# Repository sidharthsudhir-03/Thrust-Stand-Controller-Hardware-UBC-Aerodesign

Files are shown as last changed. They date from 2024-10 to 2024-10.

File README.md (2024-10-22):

# Thrust-Stand-Controller-Hardware-UBC-Aerodesign

## Overview
The **Thrust Stand Controller** is a hardware project designed for measuring motor performance parameters (thrust, torque, voltage, current) for RC aircraft. This controller helps optimize motor configurations and helps in motor selection for the UBC Aerodesign team's aircraft. The system integrates sensors and microcontroller-based data acquisition to provide reliable performance data.

## Features
- **Thrust and Torque Measurement**: Uses dual HX711 load cell amplifiers to measure thrust and torque from the motor.
- **Power Monitoring**: Integrated voltage and current sensors for real-time power consumption analysis. It is rated for 33V and 55A.
- **Microcontroller (ATMEGA32U4-AU)**: Responsible for interfacing with sensors and controlling PWM signals for the motor's ESC.
- **USB-C Connector**: Provides both power supply and data transfer capabilities.
- **ESC PWM Control**: Allows real-time adjustments of motor speed during tests via a 2-pin header for PWM control.
- **Flexible Design**: Added GPIO pin headers and solder pads for easy expansion and motor connection.

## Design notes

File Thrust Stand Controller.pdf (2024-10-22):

# THRUST STAND CONTROLLER

## Overview

The purpose of the thrust stand controller is to provide detailed measurements of motor performance which helps in motor selection for the aircraft. This controller can measure voltage, current, torque and thrust and can potentially take up to 33V and 55A. The schematic overview of the thrust stand controller is as follows:

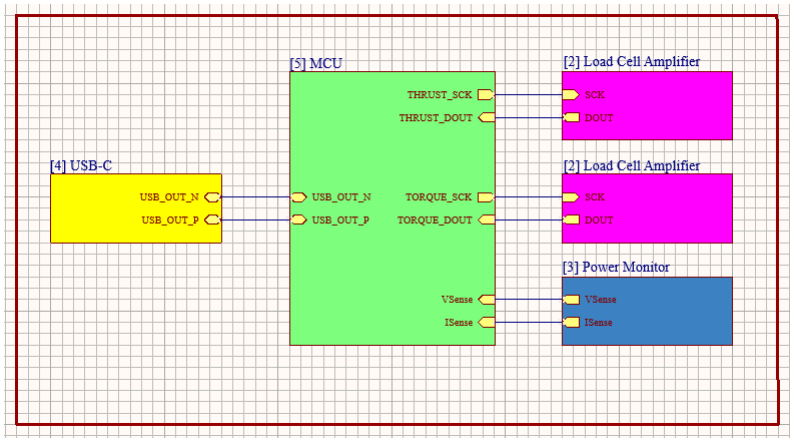
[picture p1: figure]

Fig 1: Top Level Overview of the Schematic
- USB-C: We will be using a USB-C connection for powering up the board and data logging.
- HX711 Load Cell Amplifier: There are two HX711 load cell amplifiers responsible for torque and thrust measurements. Each HX711 measures minute changes in resistance in the load cells, which are directly proportional to the force (thrust or torque). The digital output from the HX711 is fed into the microcontroller for further processing.
- Power Monitor: The power sensor uses a voltage divider circuit followed by an op-amp, which conditions the signal before sending it to the microcontroller's ADC for voltage measurement and a current sense amplifier, which senses the voltage drop across a shunt resistor and amplifies the differential signal to be sent to the microcontroller's ADC, for the current measurement.
- ATMEGA32U4-AU MCU: The ATMEGA32U4-AU microcontroller handles data acquisition from sensors and interfaces with the USB-C. It reads all the signals from the external circuits and processes them. The microcontroller also provides the necessary clock signals for the load cell ADCs (TORQUE_SCK and THRUST_SCK), ensuring synchronized data sampling for both torque and thrust measurements.
- Connections: We have the following connections in the circuit:
- There are 2x11P Male Header Pins on the board for accessing the GPIO pins of the microcontroller, providing flexibility for future expansion, testing or debugging.
- There is a 2P Male Header Pin for sending PWM control directly from the microcontroller to the ESC. One of the pins will be connected to ground.
- There are 2 pairs of solder pads to connect the Power Limiter and the ESC.

The diagram below shows how the thrust stand controller interfaces with external components of the plane’s power system for motor testing:

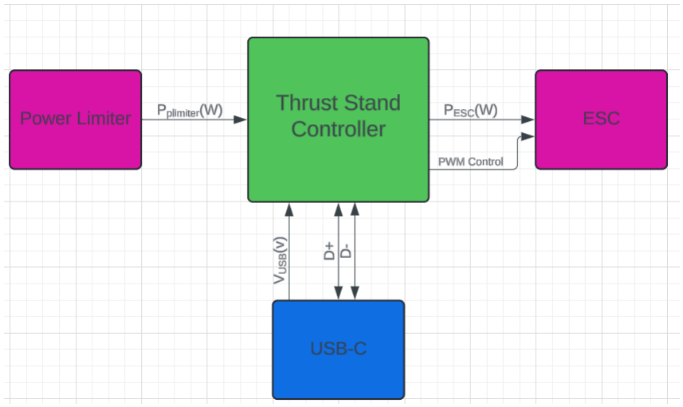
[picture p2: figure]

Fig 2: Thrust Stand Controller Connection Interface with External Hardware

## Sub Circuitry

In the following section, we will go over the main sub circuits of the thrust stand controller in detail and justify design decisions.

### 1. Load Cell Amplifier

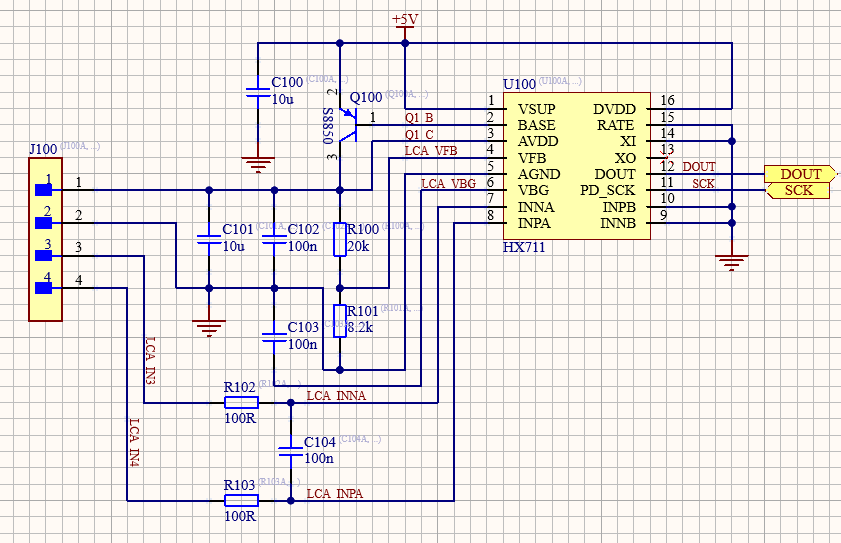
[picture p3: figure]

Fig 3: Load Cell Amplifier Schematic
The load cell amplifier is inspired by the circuitry suggested for the HX711 ADC in the datasheet (Fig.1 and Fig.4 in [1]).

The recommended component values for most of the components in the load cell amplifier is given in the datasheet as well. The only thing needed to be identified is the values of the voltage divider network (R100 and R101 in this diagram). The voltage divider network is crucial for setting the AVDD voltage of the HX711 and the formula is given by:

V

AVDD = V
BG

*

(R

100+R
101

)
R
101

VBG is 1.25V [1]. With the resistor network chosen, we get AVDD voltage as 4.3V, which is suitable for powering the analog portion of the HX711 since it must be slightly lower than VSUP (by at least 100mV) for proper operation [1]. Also note, the formula given for AVDD is incorrect and has

R101 and R100 swapped [2]. The clock for the HX711 will be fed by a GPIO pin of the microcontroller.

### 2. Power Monitor

The power monitor circuitry consists of a voltage sensor and a current sensor which sends data signals to the microcontroller for power measurement. We use solder pads to interface the power limiter and ESC with the microcontroller. The voltage and current from the power limiter is fed into the power monitor and the ESC in this scenario is treated as a load.

a. Voltage Sensor

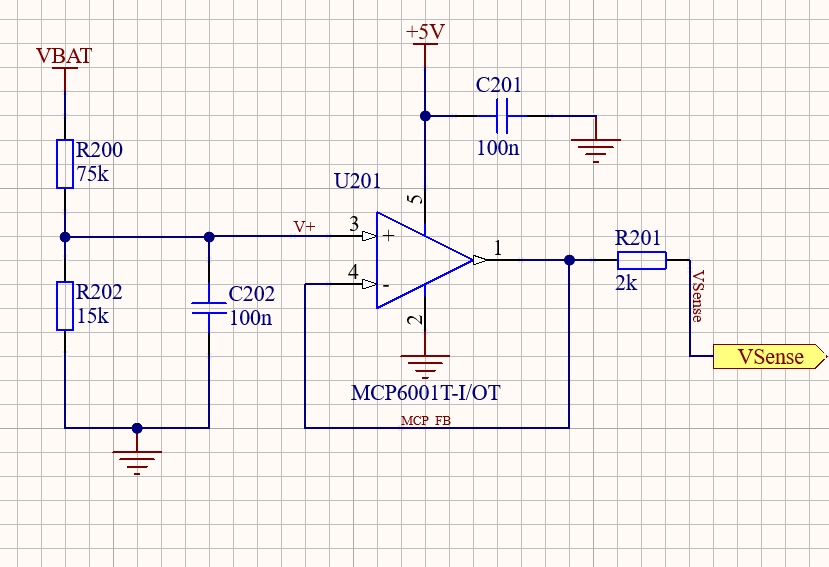
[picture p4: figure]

Fig 4: Voltage Sensor Schematic
The schematic of the voltage sensor consists of a simple voltage divider network followed by a voltage follower circuit and an additional resistor. The values of the voltage divider network was chosen in such a way that the high and low voltage levels of the input (which corresponds to a 6S LiPo) was easily detected by the microcontroller. In other words, we need to scale down a full charge and low charge 6S to a voltage level in the range of 2.7-5.5V (operating voltage range of the microcontroller (Page 2 of [3])). The voltage divider network gives us a scaling ratio of ⅙. This means:

V

VSENSE = V
BAT

*

R
202
R

200+R
202

=

V
BAT
6

A 6S LiPo at full charge is 25.2V and at low charge is 19.2V. When passed through this circuit, we get estimated values for VSense to be 4.2V and 3.2V respectively. With these calculations, we can expect the circuit to take up to 33V maximum (since the microcontroller supports up to 5.5V) This can be backed up by the spice simulations conducted:

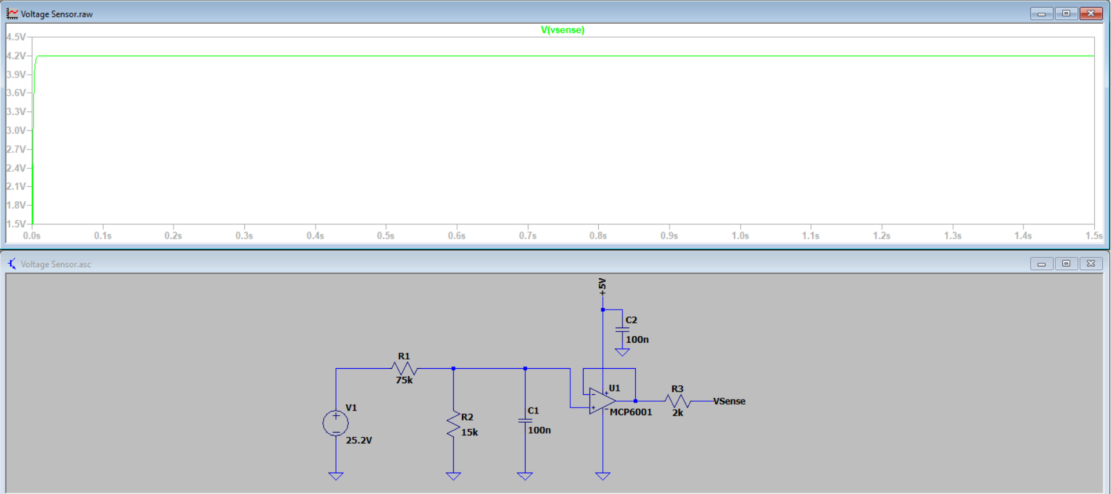
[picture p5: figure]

Fig 5: LTSpice Simulation for Voltage Sensor at 25.2V

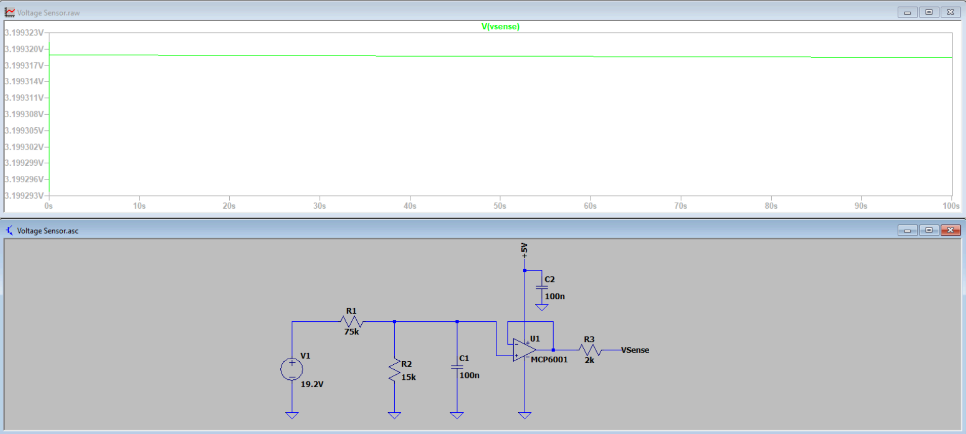
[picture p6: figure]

Fig 6: LTSpice Simulation for Voltage Sensor at 19.2V
The purpose of the capacitor is for decoupling purposes at the input of the opamp. The purpose of the voltage follower and the 2kOhm resistor is to transmit the scaled voltage to the microcontroller with as minimal current as possible since the microcontroller pins can take up to a few milliamps. The voltage follower helps in achieving this and the resistor just serves as extra protection. While we can expect some voltage drop across the resistor as a consequence, this voltage drop is minimal since we can expect the output of the voltage follower to be the transmitted voltage with minimal current. This additional circuitry allows us to detect the voltage coming in from the power limiter without damaging the microcontroller.

b. Current Sensor

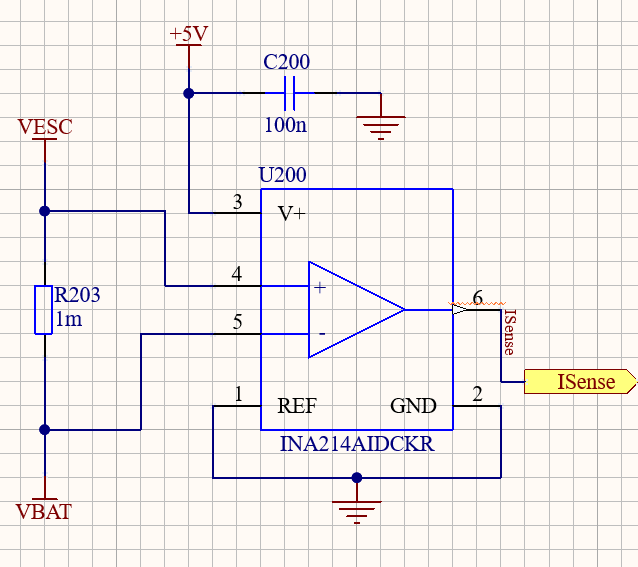
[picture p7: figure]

Fig 7: Current Sensor Schematic

The schematic of the current sensor consists of a shunt resistor followed by a current sensing amplifier (INA214AIDCKR). This current sensing amplifier has a gain of 100 V/V (Pg.1 of [4]) and follows the following formula for the output voltage:

V

ISENSE = (I
BAT

* R
203

* Gain) + V

REF = 0. 1 * I
BAT

R203 is chosen as 1mOhm as it provides a good balance between maximizing current input that is readable for the microcontroller and ease of calculation. With the formula given for voltage of Isense, we can conclude that the maximum amount of current that can be detected by the microcontroller would be 55A. Furthermore, the shunt chosen is rated for 6W and on performing power calculations for maximum current flowing into the shunt, we see:

P

SHUNT = (I
BAT

2
* R
203

) = 55

2
* 0. 001 = 3. 025W

The power consumed is well within the range of the shunt’s power rating, making it an appropriate choice for this design. Lastly, since we are only concerned with the unidirectional current coming in from the power limiter to the current sense amplifier, we connect the REF pin to ground (Pg. 20 [4]).

### 3. USB-C Connection

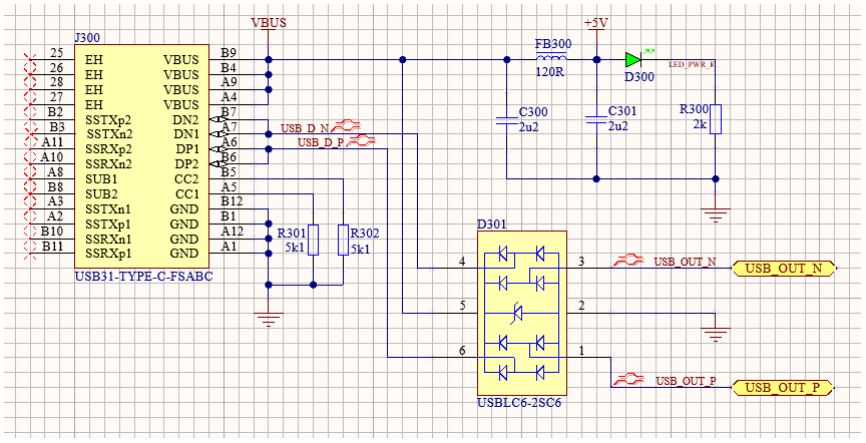
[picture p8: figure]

Fig 7: USB-C Connector Schematic
The USB-C Connector schematic consists of our USB-C connector paired with an ESD protection device at the differential pair lines. The power pin of the USB-C is connected to a pi filter, which serves to reduce noise at the power supply and improve the quality of power delivered to the circuit. Furthermore, an LED circuit is added at the end of the pi filter to indicate whether the circuit is being powered by the 5V coming out of the USB-C. Lastly, the USB-C is configured for USB 2.0 communication.

### 4. ATMEGA32U-AU Microcontroller

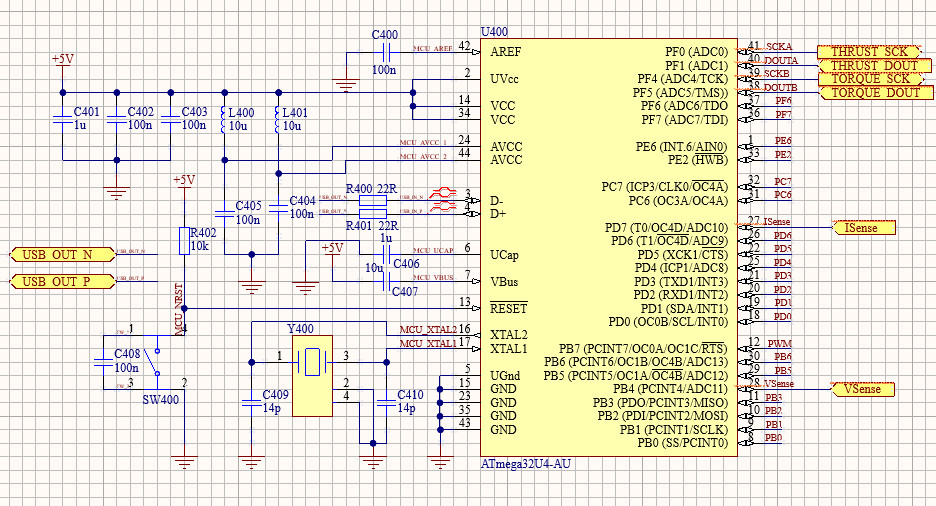
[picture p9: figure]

Fig 8: ATMEGA32U4-AU Schematic

The ATMEGA32U4-AU schematic consists of the microcontroller with its peripheral connections. The justifications for all the peripheral connections with reference to the datasheet is given below:
- 2 x 100nF capacitors at the VCC pins as standard practice
- 2 x LC Filters consisting of a 10uH inductor and 100nF capacitor connecting to each AVCC pin to eliminate noise (Section 24.7.2 of [3])
- 2 x 22 Ohm resistors connected in series with the differential pair pins (Section 21.5 of [3])
- 1 x 1uF capacitor connected to ground at UVCC (Section 21.5 of [3])
- 1 x 1uF capacitor connected to ground at UCAP (Section 21.5 of [3])
- 1 x 10uF capacitor connected to 5V at VBus (Section 21.5 of [3]). It is necessary to have a VBUS connection because it can help detect USB connection in the microcontroller (Section 21.11 of [3])
- A 5V active low logic connection for the RESET pin (Section 26.6.2 of [3])

- A 16MHz crystal oscillator with 14pF capacitors. The load capacitance of the crystal is 10pF and the shunt capacitance is 3pF [5]. We can assume the stray capacitance to be anywhere from 2pF to 5pF, so for the sake of convenience, we will stick to the stray capacitance being equal to the shunt capacitance (i.e. 3pF) [6]. This gives us the external load capacitance as [6]:

C

EXT = 2 * (C

LOAD − C
STRAY

) = 2 * (10 − 3) = 14pF

## References

[1] HX711 Datasheet: 24-Bit Analog-to-Digital Converter (ADC) for Weigh Scales (https://cdn.sparkfun.com/datasheets/Sensors/ForceFlex/hx711_english.pdf)
[2] Modifying the HX711 Breakout Board for 3.3V operation (https://hackaday.io/project/1741-honeybee-hive-monitoring/log/9780-modifying-the-hx711-breakout-board-for-33v-operation)
[3] ATMEGA16U4/ATMEGA32U4: 8-bit Microcontroller with 16/32K bytes of ISP Flash and USB Controller (https://ww1.microchip.com/downloads/en/DeviceDoc/Atmel-7766-8-bit-AVR-ATmega16U4-32U4_Datasheet.pdf)
[4] INA21x Voltage Output, Low- or High-Side Measurement, Bidirectional, Zero-Drift Series, Current-Shunt Monitors (https://www.ti.com/lit/gpn/INA214)
[5] TXC 7M Series SMD Crystal Datasheet (https://datasheet.ciiva.com/pdfs/VipMasterIC/IC/TXCC/TXCC-S-A0001240746/TXCC-S-A0001240746-1.pdf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)
[6] How to calculate the value of crystal load capacitors? (https://community.nxp.com/t5/LPC-FAQs/How-to-calculate-the-value-of-crystal-load-capacitors/m-p/464589)

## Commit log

2024-10-22 Create Project Logs for Thrust Stand Controller Revised
2024-10-22 Rename Thrust Stand Controller (1).pdf to Thrust Stand Controller.pdf
